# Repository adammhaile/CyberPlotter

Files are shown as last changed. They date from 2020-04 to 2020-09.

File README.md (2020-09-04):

|  **Component** | **Qty** | **Source** | **Notes** |
| :---: | :---: | :---: | :---: |
|  **Core Machine Components** |  |  |  |
|  Drag Chain | 2 | [Open Builds](https://openbuildspartstore.com/drag-chain-cable-carrier/ "Open Builds") |  |
|  3GT 20T Timing Pulley | 3 | [Open Builds](https://openbuildspartstore.com/3gt-gt2-3m-timing-pulley-20-tooth-250-bore-9mm-belt/ "Open Builds") |  |
|  1m Drag Chain | 2 | [Open Builds](https://openbuildspartstore.com/drag-chain-cable-carrier/ "Open Builds") |  |
|  3GT 9mm Belt | 8m | [RobotDigg](https://www.robotdigg.com/product/597/3GT-9mm-or-6mm-wide-open-ended-belt "RobotDigg") |  |
|  2040 1150mm Extrusion | 1 | [Misumi](Misumi "TITLE TEXT HERE") | HFS5-2040-1150 |
|  2040 1000mm Extrusion | 4 | [Misumi](Misumi "TITLE TEXT HERE") | HFS5-2040-1000 |
|  2040 Corner Brackets | 4 | [Misumi](Misumi "TITLE TEXT HERE") | HBLFSD5-SEP |
|  Nema23 1.2Nm 2.8A Motor | 3 | [omc-stepper](omc-stepper "TITLE TEXT HERE") | 23HS22-2804S |
|  DM542Y Stepper Driver | 3 | [omc-stepper](omc-stepper "TITLE TEXT HERE") |  |
|  Smoothieboard 5X | 1 | [Uberclock](Uberclock "TITLE TEXT HERE") | 3x probably fine or similar controller |
|  Meanwell LRS-350-24 | 1 |  | Can be bought as part of OpenBuilds PowerCase |
|  OpenBuilds PowerCase | 1 | [Open Builds](https://openbuildspartstore.com/powercase-kit/ "Open Builds") |  |
|  24 to 12V DC/DC Converter | 1 |  | Search for BO5-24-12 (sold under various brands) |
|  24 to 5V DC/DC Converter | 1 |  | Search for EA25-5V (sold under various brands) |
|  ExoSlide 40p | 6 | [ExoSlide](https://www.exoslide.com/products/slides/exoslide_40pc "ExoSlide") |  |
|  ExoSlide 20p | 6 | [ExoSlide](https://www.exoslide.com/products/slides/exoslide-20pc "ExoSlide") |  |
|  KW12 Micro Limit Switch | 2 |  | There are many variants. I used the one with a straight lever. But any will work. |
|  **Z Axis** |  |  |  |
|  625 Bearing | 2 |  |  |
|  LMU4 Linear Bearings | 4 |  |  |
|  100mm x 4mm Linear Rods | 2 |  | Hardened chrome steel |
|  125mm M5 threaded rod | 1 |  |  |
|  Nema 17 Motor | 1 |  | A basic ~1A model should work |
|  **Airbrush** |  |  |  |
|  M6x30 round standoff | 1 | [Amazon](https://www.amazon.com/gp/product/B07SPRRYFS/ "Amazon") |  |
|  MK8 Style Nozzle | 1 |  | Various sizes can be used for different effects |
|  M6 PTFE Fitting | 4 | [Amazon](https://www.amazon.com/gp/product/B01NANKRTD/ "Amazon") |  |
|  6x1mm O-ring | 2 |  |  |
|  24V solenoid | 1 | [Amazon](https://www.amazon.com/gp/product/B0815WY9HJ "Amazon") |  |
|  **Pen Lift** |  |  |  |
|  9g Hobby Servo | 1 |  |  |
|  90mm MGN9 Rail with H Block | 1 | [ZYLTech](http://www.zyltech.com/zyltech-mgn9-linear-rail-with-single-or-double-carriage-block/ "ZYLTech") | Custom cut option, 90mm |
|  **Camera** |  |  |  |
|  4K USB Camera | 1 | [Amazon](https://www.amazon.com/gp/product/B08BHM5TJD/ "Amazon") |  |
|  Microscope Lens | 1 | [Amazon](https://www.amazon.com/gp/product/B016NPUE9C/ "Amazon") |  |
|  **Electronic Components** |  |  |  |
|  8P8C Jack (RJ45) |  | [Digikey](Digikey "TITLE TEXT HERE") | 36-949-ND |
|  2x2 Molex Mini-Fit Jr Header |  | [Digikey](Digikey "TITLE TEXT HERE") | WM3801-ND |
|  2x2 Molex Mini-Fit Jr Crimp End |  | [Amazon](https://www.amazon.com/gp/product/B0753VW1B4/ "Amazon") |  |
|  0.1uF Radial Capacitor |  | [Digikey](Digikey "TITLE TEXT HERE") | 399-4151-ND |
|  ATTiny85 |  | [Digikey](Digikey "TITLE TEXT HERE") | ATTINY85-20PU-ND |
|  Trimpot |  | [Digikey](Digikey "TITLE TEXT HERE") | CT6ER103-ND |

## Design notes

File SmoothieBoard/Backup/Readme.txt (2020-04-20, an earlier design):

Hello and welcome to your new Smoothieboard !

You can find documentation here : http://smoothieware.org/ or on this SD card if you are offline.

To help you in your adventure, we put some files on this SD card for you.

A short guide to the folders : 

* Software contains Windows, Mac and Linux versions of Pronterface ( host software ), Slic3r ( slicing software ) and CURA ( host and slicing software ), as well as their source code, and documentation when available
* Drivers contains the drivers you must install for Windows to recognize your board, as well as some ( optional ) instructions for Linux
* Source contains the Smoothie firmware's source code
* Documentation contains a static version of the smoothieware.org website for your off-line enjoyement
* Backup-Firmware contains a copy of the firmware.bin for restoration if you flash a bad one for some reason
* Models/Calibration contains some common calibration parts
* Models/Smoothie contains various Smoothie-related parts, including enclosures

All of this is also easily available online, but these could be convenient if you don't have internet access for some reason. Or simply if you don't want to have to download something. Obviously on-line versions are prefered as they will be more up to date.

Smoothie is configured simply by editing the "config" file you can also find on this SD card, and resetting the board.

There are also guides that will help you get started : 

* http://smoothieware.org/3d-printer-guide
* http://smoothieware.org/CNC-Mill-guide
* http://smoothieware.org/laser-cutter-guide

Quick-start guide : 
 
* If you are running Windows, install the drivers ( http://smoothieware.org/windows-drivers or find them on this SD card )
* Install some host software like Pronterface or Cura ( also found on this SD card )
* Connect your USB cable to Smoothieboard and to your computer
* In your host software, check that Smoothieboard allows you to connect
* Now read the guide specific to your machine to find out how to wire it and configure it

Good practices : 
* Always check the polarity of all your connections before providing power to your Smoothieboard
* Unmount ( "eject" menu in Windows ) your Smoothieboard from your filesystem after writing something to it, and before printing with it

We hope you have incredible adventures with your Smoothieboard, we love to hear about them, don't hesitate to send us pictures or videos.
Thanks a lot for your confidence.

If you were to run into any trouble ( we hope you don't ) or need help you can't find in the documentation, here are some ways to find help : 

* On IRC ( recommended, you should get a fast answer ) : http://smoothieware.org/irc
* Forum : http://smoothieware.org/forum/c-496918/general
* Support mailing list : https://groups.google.com/forum/#!forum/smoothieware-support
* Email : wolf.arthur@gmail.com , don't hesitate

Smoothie is open-source software, and Smoothieboard is open-hardware.

Thanks again. The Smoothie team.

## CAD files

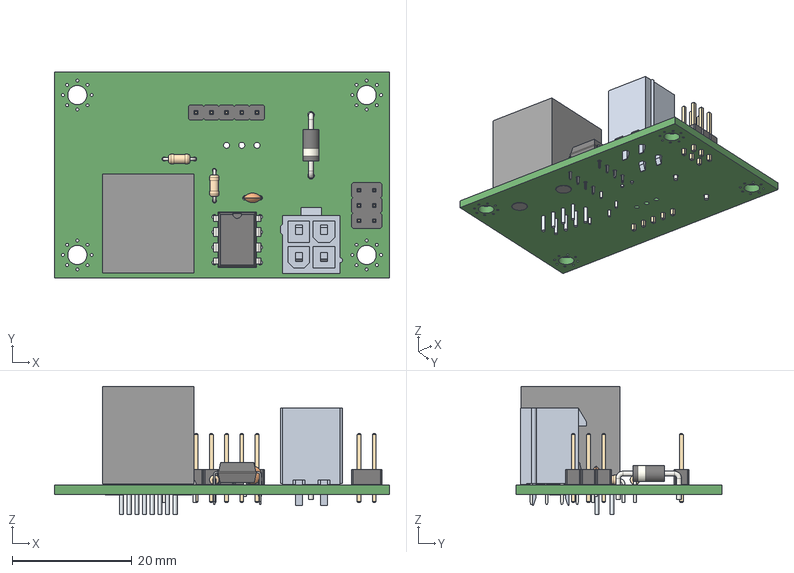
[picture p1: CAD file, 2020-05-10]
ATTinyBreakout/ATTinyBreakout.step
55.9 x 34.3 x 21.4 mm

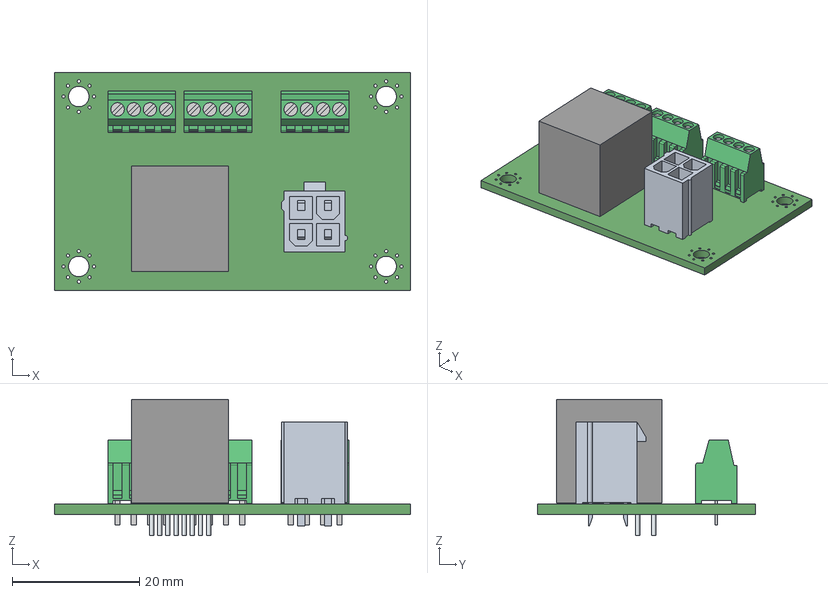
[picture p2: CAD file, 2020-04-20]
ControlBreakout/ControlBreakout.step
55.9 x 34.3 x 21.4 mm

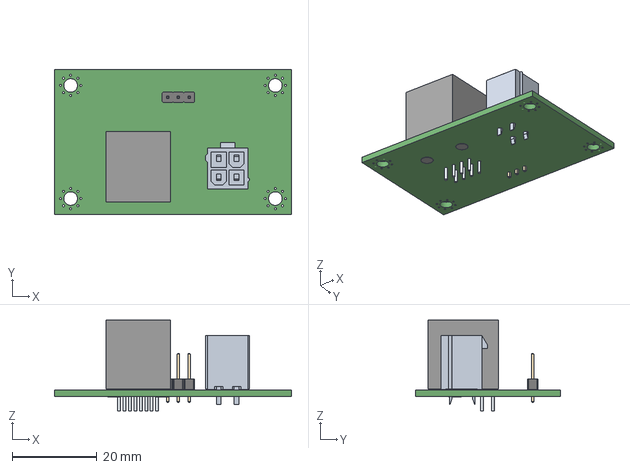
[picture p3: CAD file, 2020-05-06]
LaserBreakout/LaserBreakout.step
55.9 x 34.3 x 21.4 mm

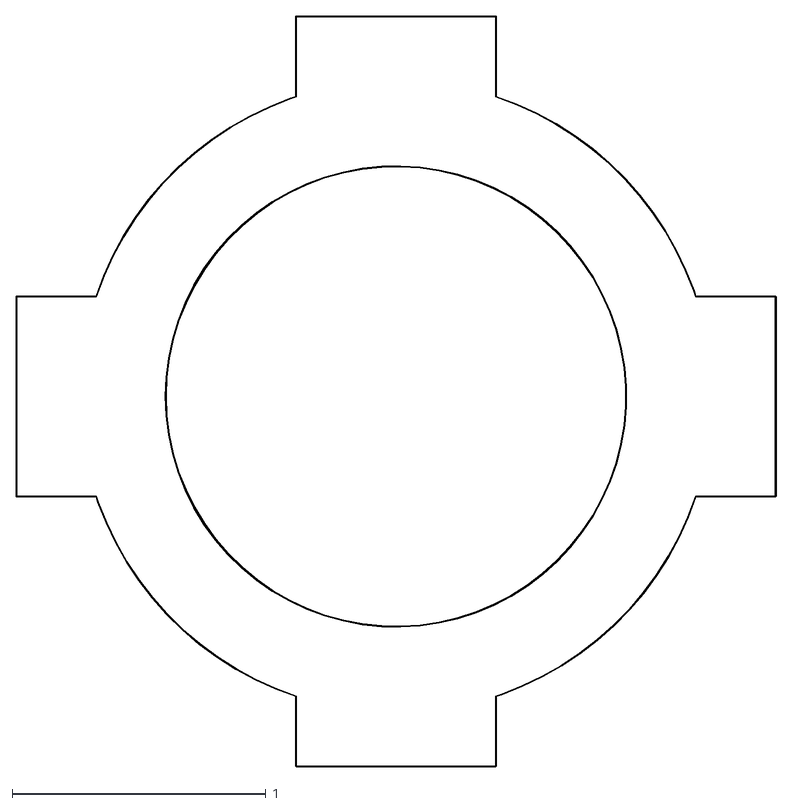
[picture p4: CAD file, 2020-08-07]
RingLight/gerb/RingLight-Edge_Cuts.dxf
2.99 x 2.95

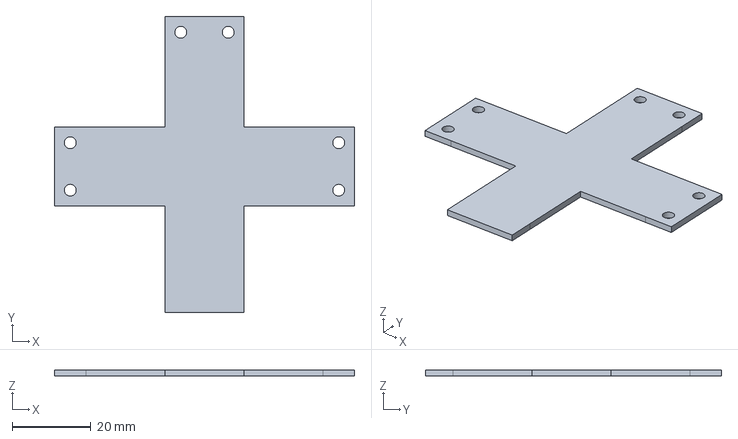
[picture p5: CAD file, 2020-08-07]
RingLight/RingLightSimple.step
76.0 x 75.0 x 1.60 mm

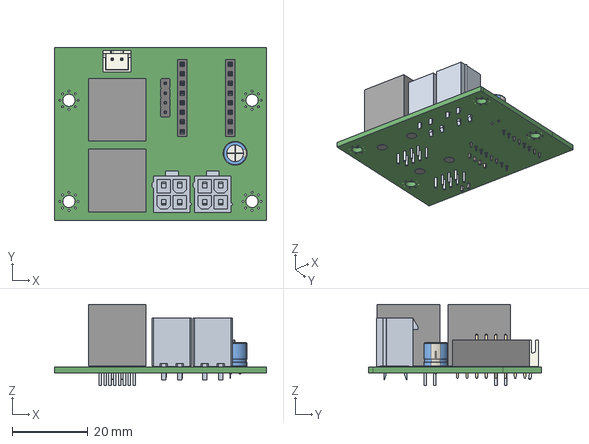
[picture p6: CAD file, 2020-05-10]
ZAxis/ZAxis.step
55.9 x 45.7 x 21.4 mm

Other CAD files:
SolenoidBreakout/SolenoidBreakout.step
RingLight/RingLight.iges
RingLight/Ringlight.dxf

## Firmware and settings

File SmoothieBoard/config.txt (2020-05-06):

# NOTE Lines must not exceed 132 characters
## Robot module configurations : general handling of movement G-codes and slicing into moves
default_feed_rate                            4000             # Default rate ( mm/minute ) for G1/G2/G3 moves
default_seek_rate                            4000             # Default rate ( mm/minute ) for G0 moves
mm_per_arc_segment                           0.5              # Arcs are cut into segments ( lines ), this is the length for
                                                              # these segments.  Smaller values mean more resolution,
                                                              # higher values mean faster computation
#mm_per_line_segment                          5                # Lines can be cut into segments ( not usefull with cartesian
                                                              # coordinates robots ).

# Arm solution configuration : Cartesian robot. Translates mm positions into stepper positions
alpha_steps_per_mm                           53.33               # Steps per mm for alpha stepper
beta_steps_per_mm                            53.33               # Steps per mm for beta stepper
gamma_steps_per_mm                           53.33               # Steps per mm for gamma stepper

# Planner module configuration : Look-ahead and acceleration configuration
planner_queue_size                           32               # DO NOT CHANGE THIS UNLESS YOU KNOW EXACTLY WHAT YOU ARE DOING
acceleration                                 3000             # Acceleration in mm/second/second.
#z_acceleration                              500              # Acceleration for Z only moves in mm/s^2, 0 uses acceleration which is the default. DO NOT SET ON A DELTA
acceleration_ticks_per_second                1000             # Number of times per second the speed is updated
junction_deviation                           0.05             # Similar to the old "max_jerk", in millimeters,
                                                              # see https://github.com/grbl/grbl/blob/master/planner.c
                                                              # and https://github.com/grbl/grbl/wiki/Configuring-Grbl-v0.8
                                                              # Lower values mean being more careful, higher values means being
                                                              # faster and have more jerk
#z_junction_deviation                        0.0              # for Z only moves, -1 uses junction_deviation, zero disables junction_deviation on z moves DO NOT SET ON A DELTA
#minimum_planner_speed                       0.0              # sets the minimum planner speed in mm/sec

# Stepper module configuration
microseconds_per_step_pulse                  1                # Duration of step pulses to stepper drivers, in microseconds
base_stepping_frequency                      100000           # Base frequency for stepping

# Cartesian axis speed limits
x_axis_max_speed                             60000            # mm/min
y_axis_max_speed                             24000            # mm/min
z_axis_max_speed                             300              # mm/min

# Stepper module pins ( ports, and pin numbers, appending "!" to the number will invert a pin )
alpha_step_pin                               2.0              # Pin for alpha stepper step signal
alpha_dir_pin                                0.5              # Pin for alpha stepper direction
alpha_en_pin                                 0.4              # Pin for alpha enable pin
alpha_current                                1.5              # X stepper motor current
alpha_max_rate                               60000.0          # mm/min

beta_step_pin                                2.1              # Pin for beta stepper step signal
beta_dir_pin                                 0.11             # Pin for beta stepper direction
beta_en_pin                                  0.10             # Pin for beta enable
beta_current                                 1.5              # Y stepper motor current
beta_max_rate                                24000.0          # mm/min

gamma_step_pin                               2.2              # Pin for gamma stepper step signal
gamma_dir_pin                                0.20             # Pin for gamma stepper direction
gamma_en_pin                                 0.19             # Pin for gamma enable
gamma_current                                1.5              # Z stepper motor current
gamma_max_rate                               300.0            # mm/min

## System configuration
# Serial communications configuration ( baud rate defaults to 9600 if undefined )
uart0.baud_rate                              115200           # Baud rate for the default hardware serial port
second_usb_serial_enable                     false            # This enables a second usb serial port (to have both pronterface
                                                              # and a terminal connected)
#leds_disable                                true             # disable using leds after config loaded
#play_led_disable                            true             # disable the play led

# Kill button (used to be called pause) maybe assigned to a different pin, set to the onboard pin by default
kill_button_enable                           true             # set to true to enable a kill button
kill_button_pin                              2.12             # kill button pin. default is same as pause button 2.12 (2.11 is another good choice)

#msd_disable                                 false            # disable the MSD (USB SDCARD) when set to true (needs special binary)
#dfu_enable                                  false            # for linux developers, set to true to enable DFU
#watchdog_timeout                            10               # watchdog timeout in seconds, default is 10, set to 0 to disable the watchdog

# Only needed on a smoothieboard
currentcontrol_module_enable                 true             #

## Extruder module configuration
extruder.hotend.enable                          false             # Whether to activate the extruder module at all. All configuration is ignored if false
extruder.hotend.steps_per_mm                    140              # Steps per mm for extruder stepper
extruder.hotend.default_feed_rate               600              # Default rate ( mm/minute ) for moves where only the extruder moves
extruder.hotend.acceleration                    500              # Acceleration for the stepper motor mm/sec�
extruder.hotend.max_speed                       50               # mm/s

extruder.hotend.step_pin                        2.3              # Pin for extruder step signal
extruder.hotend.dir_pin                         0.22             # Pin for extruder dir signal
extruder.hotend.en_pin                          0.21             # Pin for extruder enable signal

# extruder offset
#extruder.hotend.x_offset                        0                # x offset from origin in mm
#extruder.hotend.y_offset                        0                # y offset from origin in mm
#extruder.hotend.z_offset                        0                # z offset from origin in mm

# firmware retract settings when using G10/G11, these are the defaults if not defined, must be defined for each extruder if not using the defaults
#extruder.hotend.retract_length                  3               # retract length in mm
#extruder.hotend.retract_feedrate                45              # retract feedrate in mm/sec
#extruder.hotend.retract_recover_length          0               # additional length for recover
#extruder.hotend.retract_recover_feedrate        8               # recover feedrate in mm/sec (should be less than retract feedrate)
#extruder.hotend.retract_zlift_length            0               # zlift on retract in mm, 0 disables
#extruder.hotend.retract_zlift_feedrate          6000            # zlift feedrate in mm/min (Note mm/min NOT mm/sec)

delta_current                                1.5              # First extruder stepper motor current

# Second extruder module configuration
#extruder.hotend2.enable                          true             # Whether to activate the extruder module at all. All configuration is ignored if false
#extruder.hotend2.steps_per_mm                    140              # Steps per mm for extruder stepper
#extruder.hotend2.default_feed_rate               600              # Default rate ( mm/minute ) for moves where only the extruder moves
#extruder.hotend2.acceleration                    500              # Acceleration for the stepper motor, as of 0.6, arbitrary ratio
#extruder.hotend2.max_speed                       50               # mm/s
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

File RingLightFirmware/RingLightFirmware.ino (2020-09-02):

#define ADJ_IN A1 // D2
#define OUT 4

#define FILTER_COUNT 20
#define FILTER_DELAY 5

void setup()
{
    pinMode(ADJ_IN, INPUT);
    pinMode(OUT, OUTPUT);
}


void loop()
{
    static int adj_val;
    static int i;

    for(i=0; i<FILTER_COUNT; i++)
    {
        adj_val += analogRead(ADJ_IN);
        delay(FILTER_DELAY);
    }

    adj_val = adj_val / FILTER_COUNT;

    analogWrite(OUT, map(adj_val, 0, 1023, 255, 0));
}

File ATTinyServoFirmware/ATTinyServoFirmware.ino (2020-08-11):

#include <Servo.h>

#define ADJ_IN A1 // D2
#define IN 3 // A3
#define OUT 4

#define POS_OFF 0
#define POS_ON_MAX 170

#define FILTER_COUNT 8
#define FILTER_MIN   0.75
#define FILTER_DELAY 5

Servo servo;

void setup()
{
    pinMode(ADJ_IN, INPUT);
    pinMode(IN, INPUT);
    servo.attach(OUT);
    servo.write(POS_OFF);
}


void loop()
{
    static int last_pos = 255;
    static int pos;
    static float val;
    static int adj_val;
    static int i;

    val = 0.0;
    adj_val = 0;
    for(i=0; i<FILTER_COUNT; i++)
    {
        val += static_cast<float>(digitalRead(IN));
        adj_val += analogRead(ADJ_IN);
        delay(FILTER_DELAY);
    }

    val = val / FILTER_COUNT;
    adj_val = adj_val / FILTER_COUNT;

    if(val >= FILTER_MIN)
    {

        pos = map(adj_val, 0, 1023, POS_ON_MAX, POS_OFF);;
    }
    else
    {
        pos = POS_OFF;
    }

    if(pos != last_pos)
    {
        servo.write(pos);
        last_pos = pos;
    }
}

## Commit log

2020-05-06 Add more breakout boards
    [ATTinyBreakout.kicad_pcb, ATTinyBreakout.sch, LaserBreakout.kicad_pcb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]
2020-05-10 Adding ATTiny firmware
    [ATTinyBreakout.step, ZAxis.step]
2020-05-15 So many things
    [ATTinyBreakout.kicad_pcb, ATTinyBreakout.sch, ATTinyBreakout.step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]
2020-05-20 Add new solenoid breakout
    [SolenoidBreakout.kicad_pcb, SolenoidBreakout.sch, SolenoidBreakout.step]
2020-05-23 add .gitignore
    [ATTinyBreakout.kicad_pcb, ATTinyBreakout.sch, ATTinyBreakout.step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]
2020-05-24 Adding servo firmware
    [SolenoidBreakout.sch]
2020-05-24 adding delay to solenoid firmware
2020-06-11 Add adjust trimpot to attiny
    [ATTinyBreakout.kicad_pcb, ATTinyBreakout.sch]
2020-07-05 permission cleanup
    [ATTinyBreakout.kicad_pcb, ATTinyBreakout.sch, ATTinyBreakout.step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]
2020-07-06 Adding filter to servo firmware
2020-07-06 Servo trimpot adjustment
2020-08-07 Add ringlight
    [RingLight-Edge_Cuts.dxf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]
2020-08-11 Add filtering to RingLight firmware
